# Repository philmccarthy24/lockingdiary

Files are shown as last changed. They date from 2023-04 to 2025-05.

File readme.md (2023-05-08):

# Locking Diary
## DIY secure journal with numpad lock

*Phil McCarthy, May 2023*

### What is this project?

My daughter saw a diary in the toy shop with a number pad and electronic lock. I told her we weren't buying it - I could make one like that myself! She called my bluff... and didn’t forget about it. :grimacing:

So yes, making this will cost you much, much more in electronics components, 3D printing and PCB fabrication than it would cost to buy your child a cheap toy secret diary. But at least you made it yourself and had fun. :wink:

### Demo

See this video to see how the unit operates (TODO)
Instructable here: TODO

### What's included in this repository?

Original OpenSCAD designs and related assets for all parts, STL files for unmodified reprints (also Prusa project files which will save you time when slicing if you have a Prusa), KiCAD project files and gerbers for modifying/fabricating the PCB, and documentation.

Included in the documentation is [the full parts list](docs/BOM.md), [assembly instructions](docs/assembly.md), and [the printing settings that worked for me](docs/printing.md) when printing the parts out.

The rest of this readme contains information about the design choices for the project.

### Electrical Design

This is the first prototype for the electronics:

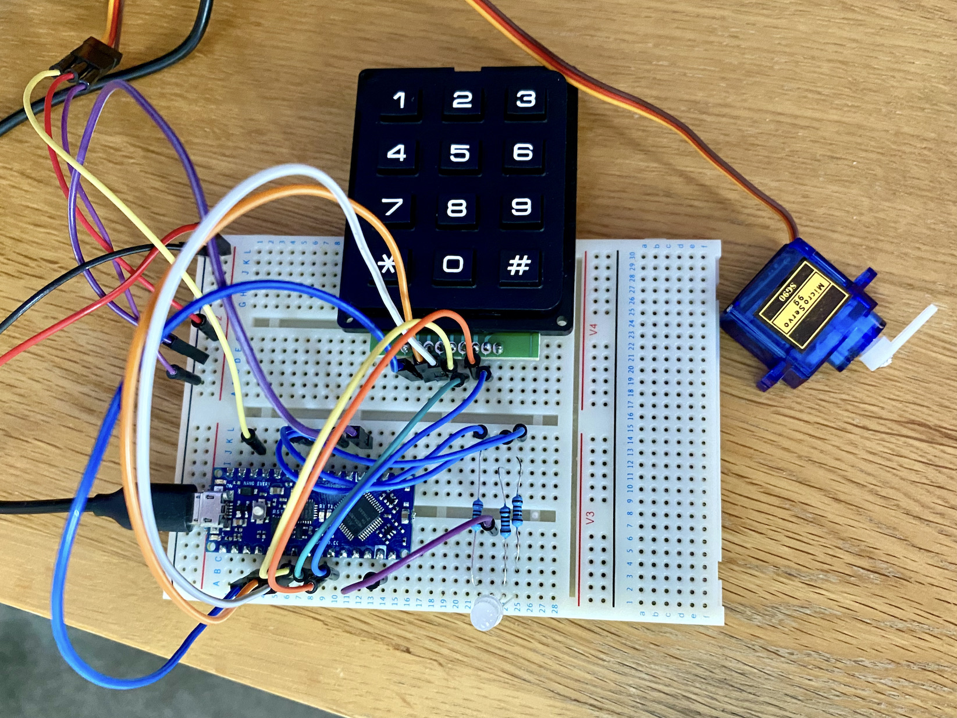
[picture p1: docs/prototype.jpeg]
prototype


An SG90 servo moving an arm 90 degrees back/forth into a recess was chosen for the lock mechanism, due to:

- low cost
- fairly electrically efficient; 750mA **stall current** at 5v (much less unencombered) vs solenoid 1A+ for *normal operation*, with excess heat generated
- easy to control, just PWM signal
- self contained vs lead screw linear actuator; don’t need driving with mosfets / driver ICs
- No additional components required

A matrix style hobbyist number pad was chosen rather than wiring 12 momentary switches up manually; bang for buck the result is tidier and more tactile.

Arduino Nano Every MCU was chosen due to:

- High pin count - need 7 pins for number pad matrix circuit alone
- ability to drive PWM at 5v without needing extra logic level conversion
- doesn’t need to be particularly fast/high powered/lots of memory.

For power, need headroom for 1A (~60mA for RGB LED, 20mA for Arduino and 750mA max for servo). To keep cost down, but battery footprint compact, AAA batteries can be positioned down the spine of the diary. An Adafruit Miniboost 5V module converts 2-6V into 5V regulated, and supplies ~1A. rechargeable AAAs are 950+mAh, 1.2vx3 = 3.6v (1100mA from Miniboost at this V) which is more than sufficient. Micro slide switch pulls the enable pin on mini boost active low / ground to stop power supply efficiently.

The Arduino's VIN pin takes 7-21v due to builtin voltage regulator. We already have a regulated 5v supply, so using the 5v output pin as an input to avoid extra DC up-conversion components as space is limited; need to make PCB as small and low profile as possible. (5v pin as input not recommended, and voltage fluctuations can lead to MCU processor damage according to forum posts, but can't source specific technical doumentation that says this can't be done with a single regulated supply where the USB won't be used in conjunction. On testing it seems to work fine).

### Firmware design

For persistent state, can use Nano Every’s EEPROM to store new pin when lock is open (by pressing # key 3 times). RGB led provides feedback about mode the lock is in - blue for “enter new pin”, green for unlocked, red for locked.

**TODO TODO TODO**

### Mechanical Design

rectangular pcb and mount / glue keypad on top. runs can be under keypad, and servo connector can be in vertical middle
pcbs mounted to book cover using M5 chicago screws, with 3D printed fascia on top

### Legal stuff
This project is not a commercial product. The designs are made available free and open source. The PCB design, CAD models and microcontroller firmware are shared under the [GPLv3 license](https://www.gnu.org/licenses/gpl-3.0.en.html). Please don't assume anything works, for any particular purpose. Built completely at your own risk.

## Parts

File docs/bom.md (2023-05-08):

#TODO

[num pad](https://shop.pimoroni.com/products/keypad-12-button-1)

Adafruit Miniboost 5V module https://www.adafruit.com/product/4654

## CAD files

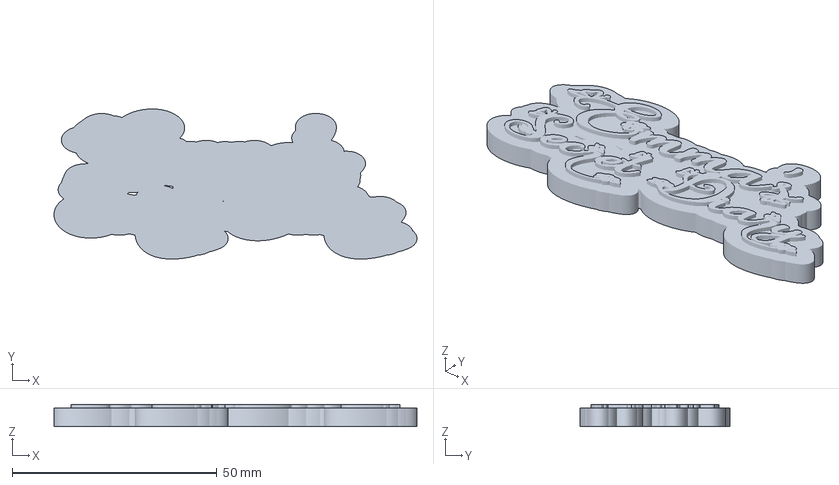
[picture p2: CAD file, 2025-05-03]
cad/stl/emma_covertext.3mf
88.7 x 36.7 x 5.40 mm

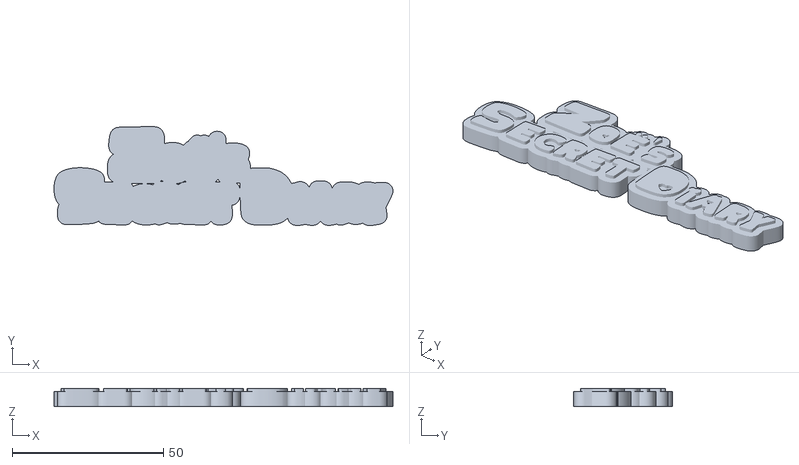
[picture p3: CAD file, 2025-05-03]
cad/stl/zoe_covertext.stl
112.2 x 32.8 x 6.00

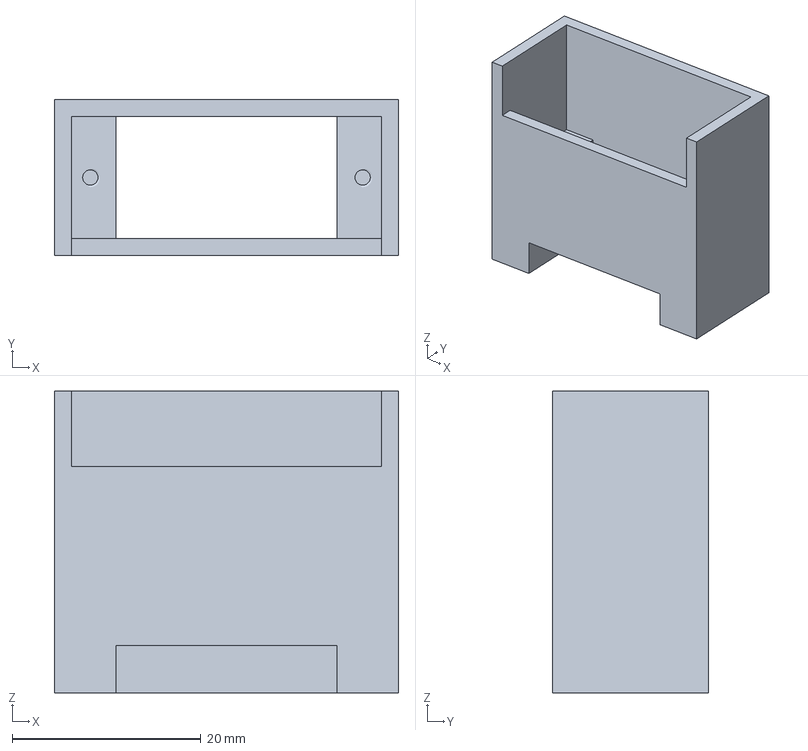
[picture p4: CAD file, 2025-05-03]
cad/stl/servo_pillar.3mf
36.5 x 16.5 x 32.0 mm

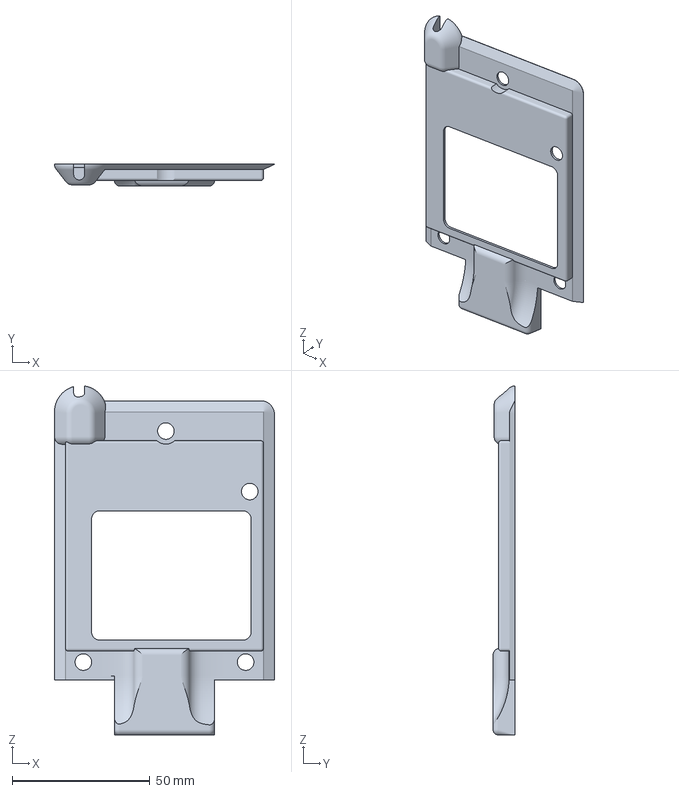
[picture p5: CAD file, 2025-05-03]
cad/stl/pcb_fascia.3mf
80.0 x 8.00 x 126.9 mm

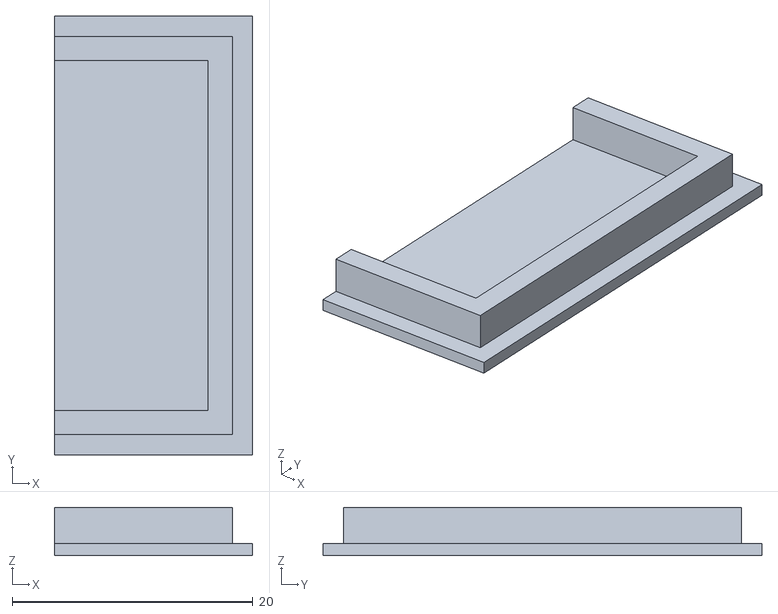
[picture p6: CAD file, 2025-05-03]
cad/stl/servo_pillar_cap.stl
16.5 x 36.5 x 4.00

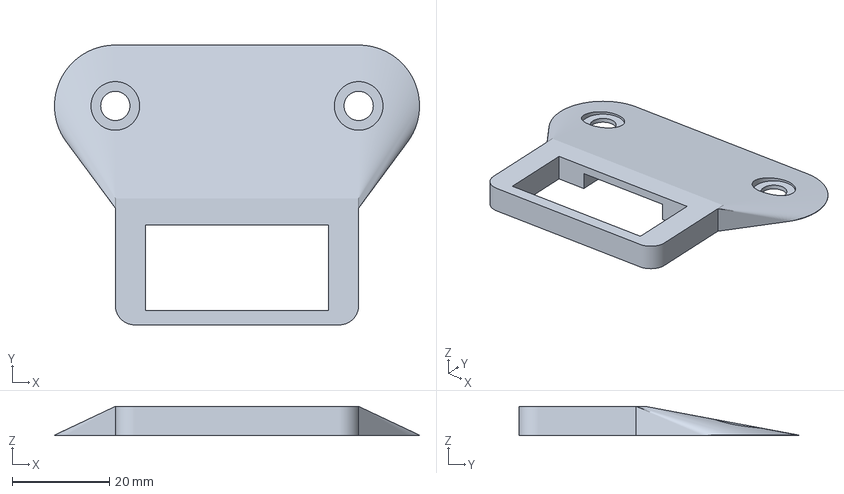
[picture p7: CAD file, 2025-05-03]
cad/stl/latch_recess_plate.3mf
75.0 x 57.5 x 6.00 mm

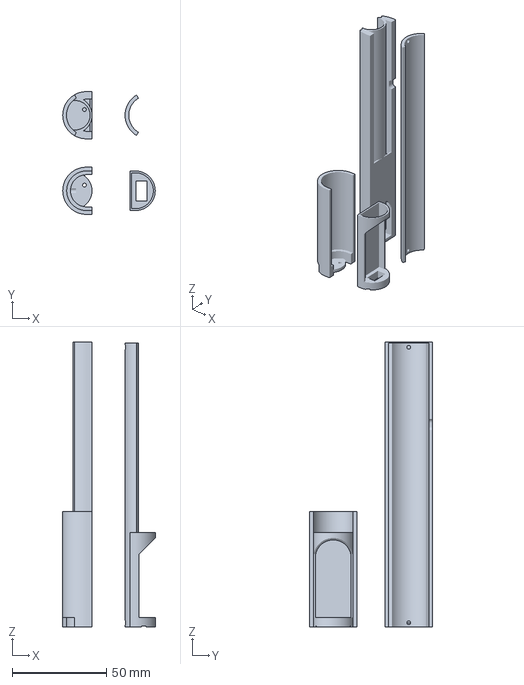
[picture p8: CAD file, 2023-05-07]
cad/stl/spine_powerpack.3mf
49.0 x 65.0 x 150.9 mm

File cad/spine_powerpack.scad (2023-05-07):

$fn=200;

// TODO: 
// way to print this is to split into two, just after neg terminal, to cut down on amount of support material required. Can then print vertically.

// 25 breadth x 212 len
// aaa 44.3 long = 133 for 3. + 5 mm for spring compression
// 10.5 d

book_length = 212;
spine_height = 25;
aaa_length = 44.3;
aaa_diam = 10.5;
spring_slop = 8;
aaa_diam_slop = 5;

bulkhead_thickness = 2;
battery_inlay_length = (aaa_length*3)+spring_slop;
neg_bulkhead_point = battery_inlay_length+10+5+bulkhead_thickness;


printing_arrangement();
//assembly();

module printing_arrangement() {
    // -ve end of power pack, put vertically for no supports
    rotate([0,-90,0])
    translate([-(battery_inlay_length+10),0,0])
    difference() {
        powerpack_base();
        translate([-1,0,0]) rotate([0,90,0]) cylinder(h=battery_inlay_length+10+1,d=spine_height*2);
    }
    
    // +ve end of power pack, put vertically for minimal supports
    translate([0,40,0])
    rotate([0,-90,0])
    difference() {
        powerpack_base();
        translate([neg_bulkhead_point-5-2,0,0]) rotate([0,90,0]) cylinder(h=100,d=spine_height*2);
    }
    
    // -ve end insert, to be glued in place
    translate([20,0,book_length-neg_bulkhead_point-4]) rotate([0,90,0]) miniboost_insert();
    
    translate([30,40,0]) lid();
}

module assembly() {
    powerpack_base();
    translate([neg_bulkhead_point,0,0]) miniboost_insert();
    //translate([5+0.25,0,3]) rotate([0,90,0]) lid();
}


// housing for miniboost, switch and wiring that slides/glues into place
module miniboost_insert() {
    // the miniboost needs 12 x 18.
    // M2.5 screw hole is 2.5x2.5 in from top left edge. Think just gluing a small nylon standoff is acceptable/easiest.
    
    // switch dimensions:
    //20 x 4.5 screw plate
    //10.6 x 6 len by width terminal case. 5mm depth + plate (0.5 thick).
    // depth including switch itself is 8.5. so could do with being recessed by 4mm
    
    // Wago 221 is 30x18x8 - not going to fit. just solder wires instead.
    translate([0,-(spine_height-4)/2,0]) cube([book_length-neg_bulkhead_point-4,spine_height-4,1]);
    difference() {
        batt_housing_outer(book_length-neg_bulkhead_point-4,3,spine_height-4);
        // hollow out center
        translate([-0.1,0,0]) batt_housing_outer(book_length-neg_bulkhead_point-4-5+0.1,3,spine_height-6);
        // take off top, leaving rear 45 degree arch
        translate([-1,-(spine_height-4)/2,5]) {
            translate([spine_height/2,0,0]) cube([book_length-neg_bulkhead_point-4-5-spine_height/2+1,spine_height-4,spine_height]);
            translate([spine_height/2,-2,0]) rotate([0,-45,0]) cube([spine_height,spine_height,spine_height]);
        }
        // hole to mount power switch
        translate([book_length-neg_bulkhead_point-4-6,-10.6/2,spine_height/4-6/2]) cube([7,10.6,6]);
        // power switch plate - might need trimming
        translate([book_length-neg_bulkhead_point-4.5,-20/2,spine_height/4-4.5/2]) cube([1,20,4.5]);
    }
}


module powerpack_base() {
    difference() {
        batt_housing_outer(book_length,3,spine_height);
        translate([10,0,(aaa_diam+aaa_diam_slop)/2+1]) housing_inlay(battery_inlay_length,aaa_diam+aaa_diam_slop);
        
        //gap for lid.
        translate([5,0,3]) rotate([0,90,0]) lid_outer(0.1);
        
        //inside volume
        inside_volume();
        //2mm extra height/diameter at switch end
        translate([neg_bulkhead_point,0,-0.1]) batt_housing_outer(60,3,spine_height-4);
        
        // holes for M2 knurl nuts, to screw lid into
        //3.5d x 4mm len for whole fixing - so 2.75 diam for melt?
        translate([battery_inlay_length+10+5/2,0,(aaa_diam+3)-5]) cylinder(h=6,d=2.75);
        translate([5+5/2,0,(aaa_diam+3)-5]) cylinder(h=6,d=2.75);
        
        // holes for terminal wires
        translate([battery_inlay_length+10-1,3,3+1]) rotate([0,90,0]) cylinder(h=5, d=2);
        translate([5+5-3,3,3+1]) rotate([0,90,0]) cylinder(h=5, d=2);
        
        // hole for power cable egress
        translate([book_length/2,spine_height/2+1,0]) cable_egress_volume();
        
        // labels for polarity
        translate([20,-4.5,0.8]) linear_extrude(10) text("+");
    translate([neg_bulkhead_point-5-bulkhead_thickness-20,-4.5,0.75]) linear_extrude(10) text("-");
    }
    
    
    
    // additional +ve end glue support, with arc for supportless printing
    difference() {
        translate([20,-spine_height/2,0]) cube([40,spine_height,1]);
        translate([20,0,-spine_height/2]) cylinder(h=spine_height, d=spine_height-8);
    }
    
}






module cable_egress_volume() {
    rotate([90,0,0])
    linear_extrude(6)
    hull() {
        circle(d=4);
        translate([2,0]) circle(d=4);
    }
}
    

module inside_volume() {
    difference() {
        translate([2,0,-0.1]) batt_housing_outer(book_length,3,spine_height-8);
        translate([8,0,(aaa_diam+aaa_diam_slop+4)/2]) housing_inlay(battery_inlay_length+4,aaa_diam+aaa_diam_slop+4);
    }
}

module lid() {
    difference() {
        lid_outer(0, 1, 0.5);
        // holes for M2 screws
        translate([-spine_height/2-1,0,(5/2)-0.25])
        rotate([0,90,0]) {
            cylinder(h=6, d=2);
            cylinder(h=2, d=4);
        }
        translate([-spine_height/2-1,0,(aaa_length*3)+spring_slop+10-(5/2)-0.25])
        rotate([0,90,0]) {
            cylinder(h=6, d=2);
            cylinder(h=2, d=4);
        }
    }
    
}

module lid_outer(z_slop, axial_slop=0, side_slop=0) {
    linear_extrude((aaa_length*3)+spring_slop+10-side_slop)
circle_section(spine_height+z_slop,4+z_slop,30+axial_slop);
}


module batt_housing_outer(length,base_height,width){
    translate([0,-width/2,0]) cube([length,width,base_height]);
    translate([0,0,base_height])
    rotate([0,90,0]) difference() {
        cylinder(h=length, d=width);
        translate([0,-width,-1]) cube([width,width*2,length+2]);
    }
}

module housing_inlay(length,diam) {
    rotate([0,90,0]) hull() {
        cylinder(h=length, d=diam);
        translate([-diam*5,0,0]) cylinder(h=length, d=diam);
    }
}

module circle_section(d,thickness,angle) {
    difference() {
        circle(d=d);
        circle(d=d-thickness);
        rotate([0,0,angle]) square([d,d]);
        rotate([0,0,270-angle]) square([d,d]);
        translate([0,-d]) square([d,d*2]);
    }
}

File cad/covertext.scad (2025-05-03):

$fn=100;

/*
linear_extrude(5) scale([0.6,0.5]) offset(r = 4) import(file="title.svg", center=true);
linear_extrude(6) scale([0.6,0.5]) offset(r = 0.5) import(file="title.svg", center=true);
*/

translate([0,50]) {
linear_extrude(5) scale([1,0.65]) offset(r = 5) import(file="title2.svg", center=true);
linear_extrude(6) scale([1,0.65]) offset(r = .4) import(file="title2.svg", center=true);
}

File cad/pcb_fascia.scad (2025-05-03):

use <threadlib/threadlib.scad>

$fn=200;

servo_gap = 5;
pcb_dims = [95,70,1.2];
servo_dims = [12.5,32.5,33];
servo_enclosure_thickness = 2;
lock_recess_height = 6;
diary_height = 26;
servo_pillar_footprint=[servo_dims.x+servo_enclosure_thickness*2,servo_dims.y+servo_enclosure_thickness*2];

//assembly();
print_layout();

module assembly() {
    /*
    color([0,1,0]) pcb();
    
    color([1,0,0]) servo();
    color([0,0,1])diary();
    
    fascia();
    
    translate([pcb_dims.x+servo_gap,(pcb_dims.y-servo_dims.y)/2-servo_enclosure_thickness,-servo_dims.z+1]) servo_pillar();
    */
    translate([pcb_dims.x+servo_gap,(pcb_dims.y-servo_dims.y)/2-servo_enclosure_thickness,-servo_dims.z]) servo_pillar_cap();
    
    //translate([0,0,-diary_height-7]) lock_recess_plate();
}

module print_layout() {
    //translate([0,0,servo_dims.z-1]) rotate([180,0,0]) servo_pillar();
    
    translate([-30,0,lock_recess_height]) rotate([180,0,0]) lock_recess_plate();
    
    //servo_pillar_cap();
}

// relative to pcb lower bottom edge
module lock_recess_plate() {
    slop=0.5;
    
    difference() {
        union() {
            translate([pcb_dims.x,(pcb_dims.y-50)/2,0]) curved_cube([25,50,lock_recess_height], 4, [true,false,true,false]);
            
            hull() {
                translate([pcb_dims.x-20,0,lock_recess_height-0.1]) {
                    translate([0,10,0]) cylinder(h=0.1,d=25);
                    translate([0,pcb_dims.y-10,0]) cylinder(h=0.1,d=25);
                }
                translate([pcb_dims.x-1,(pcb_dims.y-50)/2,0]) cube([2,50,lock_recess_height]);
            };
        }
        
        ///// cutouts
        
        // chicage screws
        translate([pcb_dims.x-20,0,-1]) {
            // mounting plates
            translate([0,10,0]) cylinder(h=lock_recess_height,d=10);
            translate([0,pcb_dims.y-10,0]) cylinder(h=lock_recess_height,d=10);
            
            // m5 bores
            translate([0,10,0]) cylinder(h=lock_recess_height+3,d=6);
            translate([0,pcb_dims.y-10,0]) cylinder(h=lock_recess_height+3,d=6);
        }
        
        // void for servo pillar
        translate([(pcb_dims.x+servo_gap)-slop,((pcb_dims.y-servo_pillar_footprint.y)/2)-slop,-1])
        cube([servo_pillar_footprint.x+slop*2,servo_pillar_footprint.y+slop*2,lock_recess_height+5]);
        
        // finally, the servo arm recess
        // 9mm out from servo pillar edge, 23 mm width across, reckon 1mm out from surface, a 2mm recess should be sufficient
        translate([pcb_dims.x+servo_gap-9,(pcb_dims.y-23)/2,lock_recess_height-1-3]) cube([9+2,23,3+2]);
        
    }
}

// little cap for servo pillar to hide servo when journal is open.
module servo_pillar_cap() {
    slop=0.3;
    // 1mm extra height onto pillar
    
    // pillar profile
    cube([servo_pillar_footprint.x,servo_pillar_footprint.y,1]);
    
    translate([0,servo_enclosure_thickness-slop,1])
    difference(){
        cube([servo_pillar_footprint.x-(servo_enclosure_thickness-slop), servo_dims.y+slop*2, 3]);
        
        translate([-1,2,0]) cube([servo_pillar_footprint.x-(servo_enclosure_thickness-slop)-2+1, (servo_dims.y+slop*2)-2*2, 4]);
    }
    
}

module servo_pillar() {
    
    difference() {
        // pillar profile
        cube([servo_pillar_footprint.x,servo_pillar_footprint.y,servo_dims.z-1]);
        
        // cutouts
        
        // top part of servo is 12mm wide, 23mm long, 16 mm height til servo screw plate. add 0.2 slop
        translate([servo_enclosure_thickness-0.2,servo_enclosure_thickness-0.2+((servo_dims.y-23)/2),0]) cube([servo_dims.x+0.2*2, 23+0.2*2, servo_dims.z]);
        
        // bottom part of servo
        servo_plate_height = servo_dims.z - 16;
        translate([servo_enclosure_thickness-0.2,servo_enclosure_thickness-0.2,-1]) cube([servo_dims.x+0.2*2, servo_dims.y+0.2*2,servo_plate_height + 1]);
        
        // M2 taps for servo screws - 2mm from edges in center
        translate([(servo_dims.x+servo_enclosure_thickness*2)/2,servo_enclosure_thickness-0.2+2,servo_plate_height-0.1]) tap("M2", turns=17);
        translate([(servo_dims.x+servo_enclosure_thickness*2)/2,servo_dims.y+servo_enclosure_thickness+0.2-2,servo_plate_height-0.1]) tap("M2", turns=17);
        
        // gap at bottom for servo arm
        translate([-0.1,servo_enclosure_thickness-0.2,-1]) cube([servo_enclosure_thickness*2+0.1,servo_dims.y+0.4,8+1]);
        
        // gap at top to feed connector through
        translate([-0.1,servo_enclosure_thickness-0.2+((servo_dims.y-23)/2),servo_dims.z-1-5]) cube([servo_enclosure_thickness*2+0.1,23+0.2*2,10+1]);
    }
}

module fascia() {
    
    // main profile
    difference() {
        union() {
            main_fascia_profile();
            
            // section of servo housing connected to fascia
            translate([pcb_dims.x,(pcb_dims.y-servo_dims.y)/2-servo_enclosure_thickness,0]) 
    curved_top_cube([servo_dims.x+servo_enclosure_thickness*2+servo_gap,servo_dims.y+servo_enclosure_thickness*2,8], 2);
        }
            
        
        ///// cutouts
        
        // servo header joiner cutout
        translate([pcb_dims.x-0.1, 11.5, 0.25]) servo_header_joiner_cutout();
        
        // pcb board cutout with slop
        translate([-0.2,-0.2,0]) cube([pcb_dims.x+0.5,pcb_dims.y+0.4,pcb_dims.z]);
        
        // servo with slop - at top, servo is 23mm long (then +0.5 for slop). side screw mounts then stick out (on servo pillar)
        servo_body_length = 23 + 0.5;
        translate([pcb_dims.x+servo_gap+servo_enclosure_thickness-0.2,((pcb_dims.y-servo_body_length)/2)-0.2,-servo_dims.z+1]) cube([servo_dims.x+0.4,servo_body_length+0.4,servo_dims.z]);
        
        // m5 chicago screw cutouts
        translate([6,35.5,-1]) cylinder(d=6,h=15);
        translate([6,35.5,2]) cylinder(d=9.5,h=15);
        translate([pcb_dims.x-5,pcb_dims.y-5.5,-1]) cylinder(d=6,h=15); // 5.5 from top edge
        translate([pcb_dims.x-5,5.5,-1]) cylinder(d=6,h=15);
        
        // servo socket is 12mm wide
        translate([pcb_dims.x-9,28,0]) cube([9+servo_gap+servo_dims.x+servo_enclosure_thickness+0.2,12,7]);
        // 5mm channel for servo cable
        translate([pcb_dims.x+servo_gap+servo_enclosure_thickness+((servo_dims.x-5)/2)-0.2,((pcb_dims.y-servo_dims.y)/2)-0.2,0]) cube([5,servo_dims.y/2,3]);
        
        // keypad base cutout
    translate([10+1.5,0,-2]) cube([pcb_dims.x-10-10-1.5,pcb_dims.y,5+2]); // at 10.5mm in from right edge, we're 5mm high, so come out to 10 from edge
        
        // keypad cutout
        translate([35,8.5,0]) curved_cube([47,58,7], 3);
        
        
        ////////////
        // left hand side, 6mm clearance needed from pcb bottom, from 10mm from pcb left edge
        
        // RGB LED is 6.5, 3.5 from pcb top, 28 from left edge
        translate([28,pcb_dims.y-4,-1]) cylinder(h=15, d=6);
        
        // power socket
        translate([-2,0,0]) cube([9+2,9,7]);
        
        // hole for power cable
        translate([-12,4,1.8+4/2]) rotate([0,90,0])
        hull() {
            cylinder(h=15,d=4);
            translate([10,0,0]) cylinder(h=15,d=4);
        }
    };
}

module main_fascia_profile() {
    hull() {
        translate([-5,-5,0]) curved_cube([pcb_dims.x+5+1.5,pcb_dims.y+5*2,0.1],5,[false,true,false,true]);
        translate([-1,-1,0]) cube([pcb_dims.x+2.5,pcb_dims.y+2,2]);
    }
    
    // servo socket cover section
    intersection() {
        translate([pcb_dims.x-10,11.5,1.75]) scale([1,1.5,1]) rotate([90,0,90]) linear_extrude(10) import("servo_socket_profile.svg");
        
        translate([pcb_dims.x-10,11.5-1,2]) mirror([0,1,0]) rotate([90,0,0]) curved_cube([10,6,(30*1.5)+2],2.5,[true,true,false,true]);
    }
    
    // joining section to servo housing
    translate([pcb_dims.x,(pcb_dims.y-servo_dims.y)/2-servo_enclosure_thickness,0]) cube([servo_gap,servo_dims.y+servo_enclosure_thickness*2,8]);
    
    // keyboard base - 6mm high. Enough to house MCU as well
    translate([10.5,0,1]) 
    minkowski() {
        sphere(r=1);
        cube([pcb_dims.x-10-10.5,pcb_dims.y,4]); // at 10.5mm in from right edge, we're 5mm high, so come out to 10 from edge
    };
    
    translate([-10,-3.5,0])
    power_socket_blister();
}

module power_socket_blister()
{
    // power socket blister
    // 10 x , 12mm wide, 8 high, 7 clearance
    
    difference() {
        translate([3,3])
        minkowski() {
            sphere(r=3);
            hull() {
            translate([-0.5,-1.5,0]) linear_extrude(0.1) curve_edge_rectangle([15.5,13]);
        translate([4-0.5,2,7.5-3]) linear_extrude(0.1) curve_edge_rectangle([11.5,6]);
            }
        }
        translate([-5,-5,-5]) cube([30,30,5]);
    }
}
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

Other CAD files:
cad/stl/emma_covertext.stl
cad/stl/latch_recess_plate.stl
cad/stl/pcb_fascia.stl
cad/stl/servo_pillar.stl
cad/stl/spine_powerpack.stl

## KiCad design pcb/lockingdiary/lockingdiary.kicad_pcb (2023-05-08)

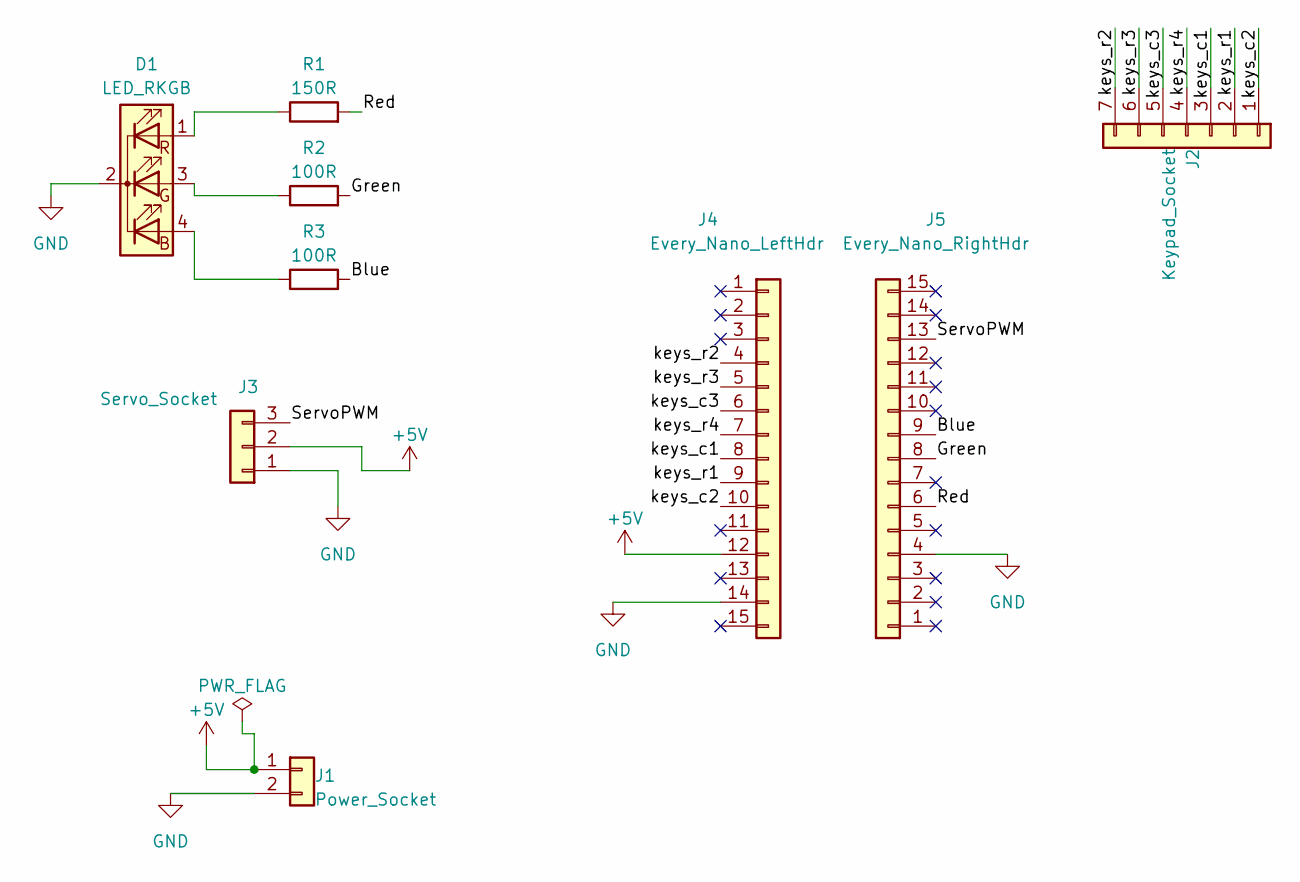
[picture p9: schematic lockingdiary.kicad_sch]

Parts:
D1: LED_RKGB; LED_D5.0mm-4_RGB
J1: Power_Socket; JST_PH_S2B-PH-K_1x02_P2.00mm_Horizontal
J2: Keypad_Socket; PinSocket_1x07_P2.54mm_Vertical
J3: Servo_Socket; JST_PH_S3B-PH-K_1x03_P2.00mm_Horizontal
J4: Every_Nano_LeftHdr; PinSocket_1x15_P2.54mm_Vertical
J5: Every_Nano_RightHdr; PinSocket_1x15_P2.54mm_Vertical
R1: 150R; R_Axial_DIN0207_L6.3mm_D2.5mm_P10.16mm_Horizontal
R2, R3: 100R; R_Axial_DIN0207_L6.3mm_D2.5mm_P10.16mm_Horizontal

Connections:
+5V: J1.1, J3.2, J4.12
/Blue: J5.9, R3.2
/Green: J5.8, R2.2
/Red: J5.6, R1.2
/ServoPWM: J3.3, J5.13
/keys_c1: J2.3, J4.8
/keys_c2: J2.1, J4.10
/keys_c3: J2.5, J4.6
/keys_r1: J2.2, J4.9
/keys_r2: J2.7, J4.4
/keys_r3: J2.6, J4.5
/keys_r4: J2.4, J4.7
GND: D1.2 (K), J1.2, J3.1, J4.14, J5.4
unnamed: D1.4 (BA), R3.1
unnamed: D1.3 (GA), R2.1
unnamed: D1.1 (RA), R1.1

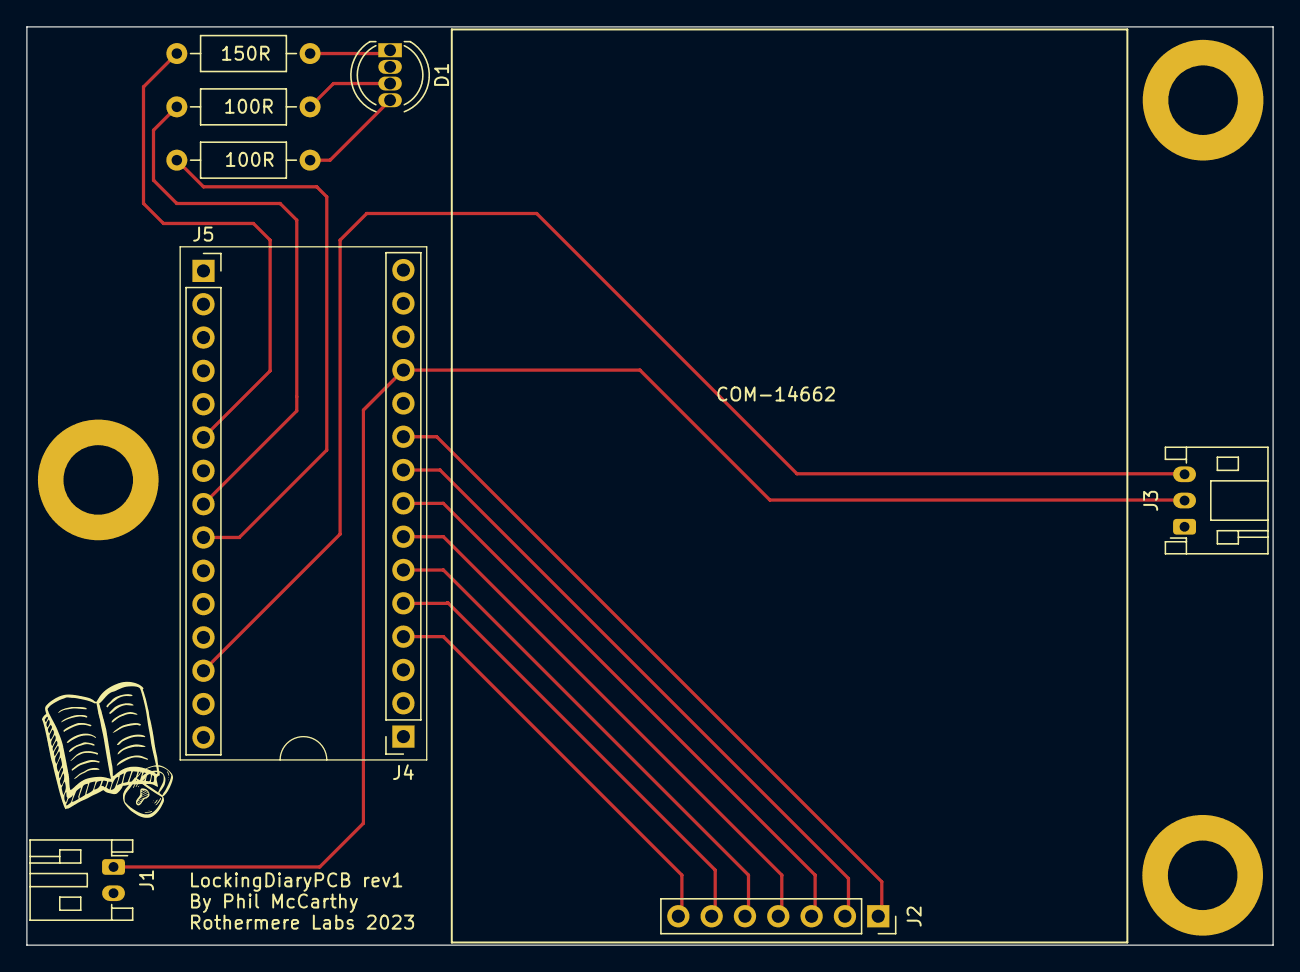
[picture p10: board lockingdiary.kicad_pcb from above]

Board: 2 copper layers, 95.0 x 70.0 mm, 9 parts (0 on the bottom side), 16 nets.

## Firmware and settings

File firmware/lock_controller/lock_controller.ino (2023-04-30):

#include "ServoLock.h"
#include "StatusLed.h"
#include "LockManagerContext.h"
#include <Keypad.h>

const byte ROWS = 4; //four rows
const byte COLS = 3; //three columns
char keys[ROWS][COLS] = {
  {'1','2','3'},
  {'4','5','6'},
  {'7','8','9'},
  {'*','0','#'}
};
byte rowPins[ROWS] = {15, 20, 19, 17}; //connect to the row pinouts of the keypad
byte colPins[COLS] = {16, 14, 18}; //connect to the column pinouts of the keypad

Keypad keypad = Keypad( makeKeymap(keys), rowPins, colPins, ROWS, COLS );

ServoLock lockDevice(10); // attach to PWM pin 10
// rgb led on pwm pins 3,5 and 6
// 3 = r (150ohm resistor needed), 5 = g (100ohm resistor needed), 6 = b (100ohm resistor needed)
StatusLed statusLed(3,5,6);
LockManagerContext lockManager(&lockDevice, &statusLed);


void setup() {
  Serial.begin(115200);
  while (!Serial) {} // wait for serial interace to connect

  lockDevice.Initialise();
  lockManager.Initialise(); // needed because we can't analogueWrite to pins before this point
}

void loop() {

  // check timeouts
  lockManager.CheckTimeout();

  char key = keypad.getKey();
  if (key){
    Serial.println(key);
    lockManager.HandleKeypress(key);
  }

  // process led updates
  statusLed.ProcessUpdate();
}

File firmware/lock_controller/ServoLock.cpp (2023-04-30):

#include "ServoLock.h"
#include <EEPROM.h>

ServoLock::ServoLock(byte pwmPin) :
m_servoPin(pwmPin)
{
  // read the last state of the lock from the EEPROM
  byte lockState = EEPROM.read(LOCK_STATE_EEPROM_ADDRESS);
  if (lockState == 0xff) {
    // eeprom hasn't been written to before - set the initial state to unlocked
    m_isLocked = false;
    EEPROM.write(LOCK_STATE_EEPROM_ADDRESS, m_isLocked);
  } else {
    m_isLocked = (bool)lockState;
  }
}

ServoLock::~ServoLock()
{
}

void ServoLock::Initialise()
{
  if (m_isLocked)
    m_servo.write(LOCK_POSITION);
  else
    m_servo.write(OPEN_POSITION);
  m_servo.attach(m_servoPin);
}

void ServoLock::Lock()
{
  m_servo.write(LOCK_POSITION);
  m_isLocked = true;
  EEPROM.update(LOCK_STATE_EEPROM_ADDRESS, m_isLocked);
}

void ServoLock::Unlock()
{
  m_servo.write(OPEN_POSITION);
  m_isLocked = false;
  EEPROM.update(LOCK_STATE_EEPROM_ADDRESS, m_isLocked);
}

bool ServoLock::IsLocked()
{
  return m_isLocked;
}

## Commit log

2023-05-07 Finished spine battery pack design. Started on PCB design
    [covertext.scad, lock_enclosure.scad, lockingdiary.kicad_pcb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]
2023-05-08 Finished rev1 PCB design. Started on readme and docs
    [covertext.scad, covertext.stl, lockingdiary.kicad_pcb]
2023-05-22 Designed fascia plate - prototype needs tweaks
    [lid.stl, pcb_fascia.scad, pcb_fascia.stl]
2025-05-03 Some design improvements for Emma's diary
    [covertext.scad, covertext.stl, emma_covertext.3mf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]
